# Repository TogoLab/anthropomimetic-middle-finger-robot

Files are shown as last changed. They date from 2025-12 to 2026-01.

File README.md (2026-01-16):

# 人体模倣中指ロボット（Anthropomimetic Middle Finger Robot）

📘 日本語版（このページ）  
🌍 [English](README_EN.md)

---
## 概要

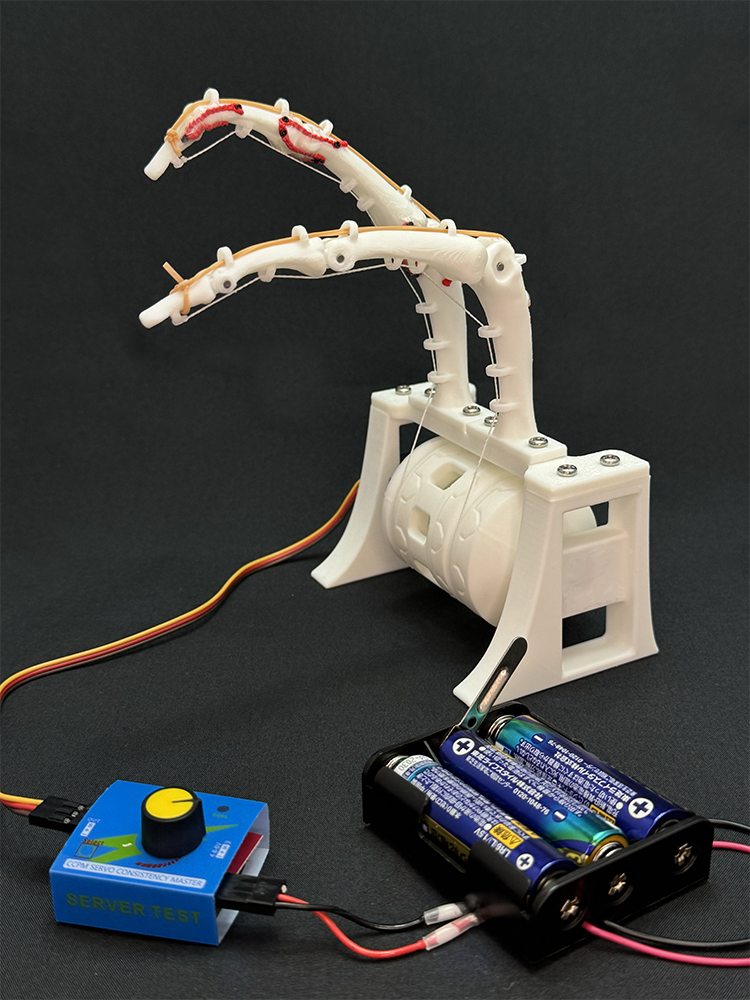
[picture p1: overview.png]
Anthropomimetic Middle Finger Robot


本リポジトリでは、**人体の中指の構造を模倣したロボット指**の  オープンハードウェア設計データを公開しています。

本プロジェクトは、  
- 人体模倣ロボット関節機構と従来ロボット関節機構の比較  
- 人体構造（骨・関節）の理解  
- 教育・体験用途  
を目的として設計されています。

本ロボットは **マイコンやソフトウェアを使用せず**、  
サーボモータ・サーボテスター・電池のみで動作します。  
そのため、ものづくりをしたことがない中学生・高校生でも扱いやすい構成になっています。
「部品を用意するのが大変だ」、「作り方を直接教えてほしい」、「お金がない」という場合には、電気通信大学で開催されている[匠ガールプロジェクトのラボ体験](http://www.ge.uec.ac.jp)や[脳・医工学研究センターのスプリングセミナー](http://blsc.xsrv.jp/)で本ロボットキットの作成体験会を実施していますので、ご参加ください。

東郷研究室では、この人体模倣中指ロボットの作り方を拡張・発展させ、様々な身体部位の人体模倣ロボットの開発に取り組んでいます。本ロボットの作成を面白いと感じたら、是非東郷研究室に参加してください。

---

## 特徴

- 人体（生物）関節を模したモデルと、回転（ロボット）関節モデルの2種類を用意
- ヒトの末節骨〜中手骨までの構造を再現
- 3Dプリント可能なSTLデータと編集可能なCADデータ（STEP）を提供
- 教育用途を想定したシンプルな構成
- ソフトウェア不要（完全ハードウェア）

---

## リポジトリ構成

```
cad/        CADデータ（STEP、F3D）
stl/        3Dプリント用STLデータ
docs/       組み立てマニュアル
licenses/   ライセンス関連ファイル
```

---

## 必要部品（BOM）

必要な部品の一覧は以下を参照してください。

- [部品表（BOM）](./BOM.md)

※ 教育用途を想定しており、同等品・代替品の使用は問題ありません。

---
## 部品の準備

### 樹脂部品の3Dプリント

Bambu Lab A1 miniでの造形を確認しています。
造形パラメータは以下のとおりです。

| フィラメント | Bambu Lab PLA Basic |
| --- | --- |
| 積層ピッチ  | 0.2 mm |
| 充填率 | 15 % |
| インフィル  | グリッド |
| ノズル | 0.4 mm |

### 靭帯の準備

鎖編みを解説する[YouTube動画](https://youtu.be/j-NHvQiJupI?si=Ml5NFn5y3y6gGRWc)などを参考に、PEワイヤを鎖編みします。
[1 mm用のレース針](https://amzn.asia/d/457qnYa)で編んでいます。
端点は結ぶか、ライターで炙って処理します。

---
## 組み立て方法

組み立て手順の詳細は、以下のマニュアルを参照してください。

- 日本語マニュアル：`docs/manual_ja.pdf`

※ 本マニュアルは体験会で配布しているマニュアルを一部改変したものです。本OSH版ではベース（右）の研究室・大学ロゴを削除しています。

---
  
## ライセンス

本リポジトリには、複数のライセンスが適用されています。  
使用する際は、対象ファイルのライセンスを必ず確認してください。

- **骨（人体）モデル**  
  - `/cad/finger_*`,  `/stl/finger_*`  
  - Creative Commons Attribution-ShareAlike 2.1 Japan (CC BY-SA 2.1 JP)  
  - 元データ：[BodyParts3D / ライフサイエンス統合データベースセンター](https://lifesciencedb.jp/bp3d/)

- **土台・プーリー等のオリジナル設計部品**  
  - `/cad/base_*`,  `/stl/base_*`  
  - Creative Commons Attribution 4.0 International (CC BY 4.0)

- **組み立てマニュアル（PDF）**  
  - © Togo Laboratory, All Rights Reserved

詳細は `LICENSE` および `licenses/` フォルダ内のファイルを参照してください。

※ 本リポジトリに含まれる研究室ロゴ・大学ロゴ・名称等は、上記ライセンスの対象外です。これらの使用には、別途許可が必要です。

---

## 注意事項・免責

- 本データは教育・研究用途を目的として提供されています。
- 本ロボットの使用・改造・配布は自己責任で行ってください。
- 可動部による指の挟み込み等に注意してください。
- 本リポジトリの内容を利用したことによるいかなる損害についても、作者は責任を負いません。

---

## 作者・連絡先

東郷 俊太  
電気通信大学大学院情報理工学研究科  
機械知能システム学専攻　准教授  
[ResearchMap](https://researchmap.jp/shuntatogo)
[東郷研究室](http://www.hi.mce.uec.ac.jp/togolab/)
[X](https://twitter.com/togo_lab/)
[Instagram](https://www.instagram.com/togolab_uec/)
[YouTube](https://www.youtube.com/channel/UC10spcvW8-pCTLKy5rrDHyw)

ご質問や不具合報告は GitHub Issues あるいはs.togo[at]uec.ac.jpまで。

東郷研究室では、教育・研究活動へのご支援も歓迎しています。
[電気通信大学基金](https://www.uec.ac.jp/kikin/archives/fund/togolab)

---

## 関連発表

 * 深代 悠太，姜 銀来，横井 浩史，東郷 俊太，“人体模倣母指CM関節の可動域と関節剛性の計測”，第43回日本ロボット学会学術講演会，2D2-01，東京科学大学大岡山キャンパス，2025年9月2–5日．
 * 永嶋 圭佑，姜 銀来，横井 浩史，東郷 俊太，”人体模倣中指ロボットのSim2Realに向けたシミュレーターと実機の開発”，ロボティクス・メカトロニクス講演会2025，2A1-J05，山形ビッグウイング，2025年6月4日–7日．
 * 工藤 陸，姜 銀来，横井 浩史，東郷 俊太，“人体を模倣した流体潤滑を有する指関節構造の粘弾性特性”，第42回日本ロボット学会学術講演会，2J3-06，大阪工業大学梅田キャンパス，2024年9月3–6日．
 * 小畑 承経，姜 銀来，横井 浩史，東郷 俊太，“人体の筋骨格構造を模倣したロボット手指・手首および前腕の開発”，ロボティクス・メカトロニクス講演会2024，2A2-J06，ライトキューブ宇都宮，2024年5月29日–6月1日．
 * 工藤 陸，姜 銀来，横井 浩史，東郷 俊太，“人体を模倣した流体潤滑を有する指関節構造の粘性特性”，ロボティクス・メカトロニクス講演会2024，1A1-D06，ライトキューブ宇都宮，2024年5月29日–6月1日．
 * 小畑 承経，姜 銀来，横井 浩史，東郷 俊太，“人体の筋骨格構造を模倣したロボット手首および前腕の開発” ，第41回日本ロボット学会学術講演会，1B3-02，仙台国際センター，2023年9月11–14日．
 * 工藤 陸，姜 銀来，横井 浩史，東郷 俊太，“人体の関節における液体潤滑を模倣した指関節構造の開発” ，第41回日本ロボット学会学術講演会，1B3-01，仙台国際センター，2023年9月11–14日．

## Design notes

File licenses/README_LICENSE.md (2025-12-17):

# License Guide (日本語)

本リポジトリは、複数のライセンスを組み合わせて構成されています。
使用する際は、対象ファイルに適用されるライセンスを必ず確認してください。

## 骨（人体）モデル
- 対象: cad/finger_* , stl/finger_*
- ライセンス: CC BY-SA 2.1 JP
- 注意:
  - クレジット表示が必要です
  - 改変・再配布時は同一ライセンス（継承）が必要です

## 土台・プーリー等のオリジナル設計部品
- 対象: cad/base_* , stl/base_*
- ライセンス: CC BY 4.0
- 注意:
  - クレジット表示のみ必要
  - 改変・商用利用も可能です

## 組み立てマニュアル
- 対象: docs/*.pdf
- ライセンス: All Rights Reserved
- 注意:
  - 再配布・改変は禁止されています

## ロゴ・名称について
研究室ロゴ、大学ロゴ、名称等は、いずれのライセンスにも含まれません。
使用には別途許可が必要です。

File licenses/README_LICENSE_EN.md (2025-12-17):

# License Guide (English)

This repository is composed of materials distributed under multiple licenses.  
Please make sure to check the license applicable to each file or directory before use.

## Bone (Human Anatomy) Models
- Scope: `cad/finger_*`, `stl/finger_*`
- License: Creative Commons Attribution-ShareAlike 2.1 Japan (CC BY-SA 2.1 JP)
- Notes:
  - Attribution (credit) is required
  - Any modified or redistributed versions must be released under the same license (share-alike)

## Original Design Parts (Base, Pulleys, etc.)
- Scope: `cad/base_*`, `stl/base_*`
- License: Creative Commons Attribution 4.0 International (CC BY 4.0)
- Notes:
  - Attribution is required
  - Modification and commercial use are permitted

## Assembly Manuals
- Scope: `docs/*.pdf`
- License: © Togo Laboratory, All Rights Reserved
- Notes:
  - Redistribution and modification are not permitted

## Logos and Names
Laboratory logos, university logos, names, and trademarks are not covered by any of the above licenses.  
Separate permission is required for their use.

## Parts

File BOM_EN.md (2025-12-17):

# Bill of Materials (BOM)

This document lists the components required to assemble the **Anthropomimetic Middle Finger Robot**.  
The design is intended for educational use, and **equivalent or alternative components may be used without issue**.

The provided links are examples of where components can be obtained and **do not imply endorsement of any specific vendor**.

---

## Required Components

| Manual ID | Component Name | Specification / Notes | Qty | Link |
| --- | --- | --- | --- | --- |
| 1-1 | Battery holder | 3 × AA batteries, with switch | 1 | https://akizukidenshi.com/catalog/g/g112240/ |
| 1-2 | Servo cable | Cut in half before use | 1 | https://amzn.asia/d/8mVq6jo |
| 1-3 | Heat-shrink solder connector | Shrink using heat gun or soldering iron | 2 | https://amzn.asia/d/0xNL0ZV |
| 2 | Controller | Servo tester | 1 | https://amzn.asia/d/4pgGVFi |
| 3 | Servo motor | SG90 | 1 | https://amzn.asia/d/4hQo8Cy |
| 7 | Dry battery | Alkaline AA | 3 | https://amzn.asia/d/7LyDhHT |
| 23,29,32  | Ligament | PE braided wire, size #5 (8 strands), red | 1 | https://amzn.asia/d/2dyn106 |
| 24,30,33  | Joint capsule sheet | Sweat-stain prevention film | 1 | https://amzn.asia/d/8erxhIF |
| 25,35 | Rubber band | Flat length 60 mm | 2 | |
| 26,36 | Muscle wire | PE braided wire, size #5 (8 strands), white | 1 | https://amzn.asia/d/3m2Y8FW |
| 27,37,39  | Tapping screw | M2.5 × 6 mm | 4 | https://amzn.asia/d/fFQeuqP |
| 28,31,34  | Tapping screw | M1 × 3 mm | 24  | https://ja.aliexpress.com/item/1005003207019640.html |
| 43 | Tapping screw | M1 × 3.5 mm | 4 | https://ja.aliexpress.com/item/1005003207019640.html |
| 38 | Shaft | M2 × 10 mm | 3 | https://amzn.asia/d/0ygpu5s |
| 40 | Bolt | M3 × 8 mm | 8 | https://amzn.asia/d/4OWtTQD |
| 41 | Nut | M3 | 8 | https://amzn.asia/d/2O0UdSI |
| 42 | Flanged bushing | 80F-0803 | 1 | https://www.monotaro.com/p/0046/0476/?t.q=80F-0803 |

---

## Tools

*The tools listed below assume a typical hobbyist or educational workshop environment.  
Equivalent tools may be used.*

| Manual ID | Tool Name | Notes | Link |
| --- | --- | --- | --- |
| a | Scissors | Any type | https://www.monotaro.com/p/5375/1733/ |
| b | Mini needle-nose pliers | Optional | https://jp.daisonet.com/products/4549131301625 |
| c | Nippers | Any type | https://ja.aliexpress.com/item/1005006129098627.html |
| d | Precision screwdriver set | Any type | https://jp.daisonet.com/products/4550480360881 |
| e | Darning needle | Optional | https://www.monotaro.com/p/3041/2795 |
| f | Tweezers (curved tip) | Optional | https://jp.daisonet.com/products/4550480538464 |
| g | Diamond file | Any type | https://jp.daisonet.com/products/4979909890288 |
| h | Cloth tape | Any type | https://www.monotaro.com/p/0671/3324/ |
| i | Pincushion | Optional | https://ec.cando-web.co.jp/item/4520297020223/ |
| j | Magnetizer | Optional | https://www.monotaro.com/p/4969/1626 |
| k | Stainless steel tray | Optional | https://jp.daisonet.com/products/4549131589962 |
| l | Magnetic sheet | Optional | https://jp.daisonet.com/products/4550480675473 |
| m | Cutting mat | Optional | https://www.monotaro.com/p/4310/0296 |

---

*This bill of materials is provided for educational and research purposes only.*  
*The authors and affiliated institutions assume no responsibility for any damage or loss resulting from the use of this document.*

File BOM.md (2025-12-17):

# 部品表（BOM）

このドキュメントは、人体模倣中指ロボットを組み立てるために必要な部品一覧です。  
教育用途を想定しており、**同等品・代替品の使用は問題ありません**。
リンク先は入手例として示したものであり、特定の販売元を推奨するものではありません。

---

## 必須部品

| マニュアル部品番号 | 部品名 | 仕様、備考 | 数量  | リンク |
| --- | --- | --- | --- | --- |
| 1-1 | 電池ボックス | 単３電池×3、スイッチ付き | 1 | https://akizukidenshi.com/catalog/g/g112240/ |
| 1-2 | サーボケーブル | 半分に切って使う | 1 | https://amzn.asia/d/8mVq6jo |
| 1-3 | 熱収縮はんだコネクタ | ヒートガンやはんだこてで収縮  | 2 | https://amzn.asia/d/0xNL0ZV |
| 2 | コントローラ | サーボテスター | 1 | https://amzn.asia/d/4pgGVFi |
| 3 | サーボモータ | SG90 | 1 | https://amzn.asia/d/4hQo8Cy |
| 7 | 乾電池 | アルカリ、単３ | 3 | https://amzn.asia/d/7LyDhHT |
| 23、29、32  | 靭帯 | 8本編5号のPEワイヤ（赤色） | 1 | https://amzn.asia/d/2dyn106 |
| 24、30、33  | 関節包シート | 汗ジミ防止フィルム | 1 | https://amzn.asia/d/8erxhIF |
| 25、35 | 輪ゴム | 折径60mm | 2 | |
| 26、36 | 筋ワイヤ | 8本編5号のPEワイヤ（白色） | 1 | https://amzn.asia/d/3m2Y8FW |
| 27、37、39  | タッピングネジ | M2.5 x 6mm | 4 | https://amzn.asia/d/fFQeuqP |
| 28、31、34  | タッピングネジ | M1 x 3 | 24  | https://ja.aliexpress.com/item/1005003207019640.html |
| 43 | タッピングネジ | M1 x 3.5 | 4 | https://ja.aliexpress.com/item/1005003207019640.html |
| 38 | シャフト | M2 x 10mm | 3 | https://amzn.asia/d/0ygpu5s |
| 40 | ボルト | M3 x 8mm | 8 | https://amzn.asia/d/4OWtTQD |
| 41 | ナット | M3 | 8 | https://amzn.asia/d/2O0UdSI |
| 42 | フランジブッシュ | 80F-0803 | 1 | https://www.monotaro.com/p/0046/0476/?t.q=80F-0803 |

---

## 工具

※ 工具は一般的な工作環境を想定した例であり、同等の工具があれば問題ありません。

| マニュアル番号 | 工具名 | 備考 | リンク |
| --- | --- | --- | --- |
| a | はさみ | なんでも良い | https://www.monotaro.com/p/5375/1733/ |
| b | ミニラジオペンチ  | あると便利  | https://jp.daisonet.com/products/4549131301625 |
| c | ニッパー | なんでも良い | https://ja.aliexpress.com/item/1005006129098627.html |
| d | 精密ドライバー | なんでも良い | https://jp.daisonet.com/products/4550480360881 |
| e | とじ針 | あると便利  | https://www.monotaro.com/p/3041/2795 |
| f | ピンセット鷲口 | あると便利  | https://jp.daisonet.com/products/4550480538464 |
| g | ダイヤモンドやすり | なんでも良い | https://jp.daisonet.com/products/4979909890288 |
| h | 布テープ | なんでも良い | https://www.monotaro.com/p/0671/3324/ |
| i | ピンクッション | なくても良い | https://ec.cando-web.co.jp/item/4520297020223/ |
| j | マグネタイザー | なくても良い | https://www.monotaro.com/p/4969/1626 |
| k | ステンレストレー  | なくても良い | https://jp.daisonet.com/products/4549131589962 |
| l | マグネットシート  | なくても良い | https://jp.daisonet.com/products/4550480675473 |
| m | カッターマット | なくても良い | https://www.monotaro.com/p/4310/0296/ |

※ 本部品表は教育・研究用途を目的として公開されています。
※ 本部品表の使用により生じたいかなる損害についても、著者および所属機関は責任を負いません。

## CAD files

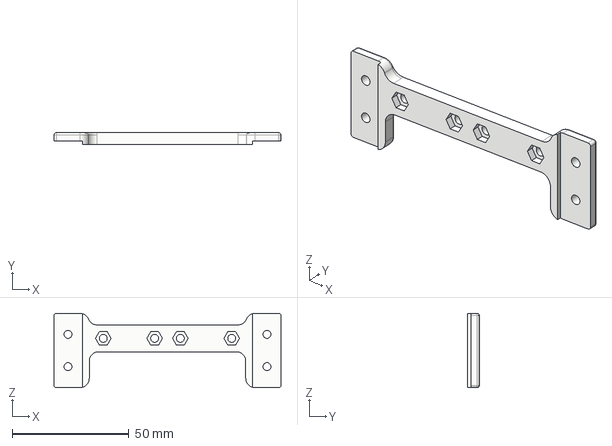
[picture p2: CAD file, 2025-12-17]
cad/base_center_plate_v1.step
97.2 x 5.00 x 31.8 mm

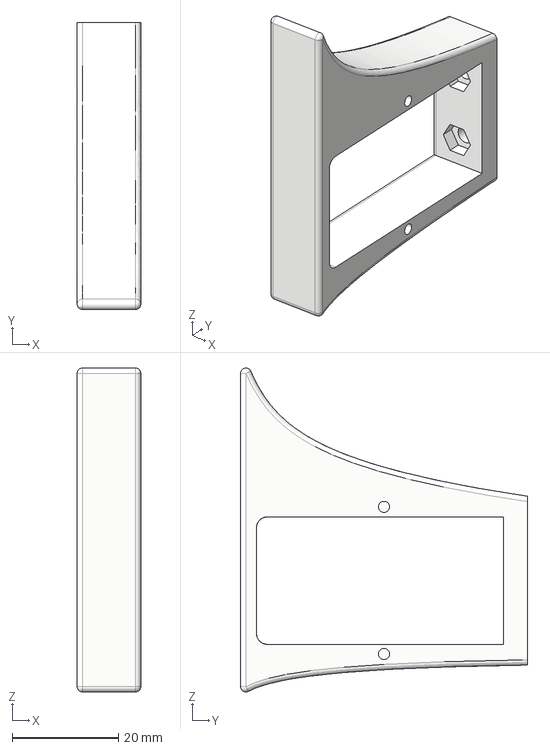
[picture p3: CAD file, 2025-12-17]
cad/base_left_foot_v1.step
12.0 x 54.0 x 61.0 mm

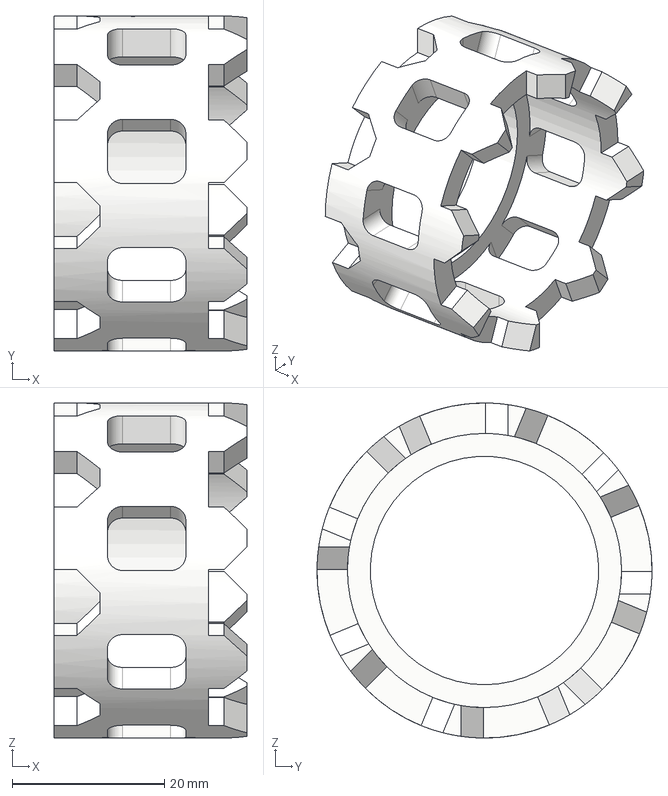
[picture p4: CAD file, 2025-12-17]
cad/base_pulley_2_v1.step
25.3 x 44.0 x 44.0 mm

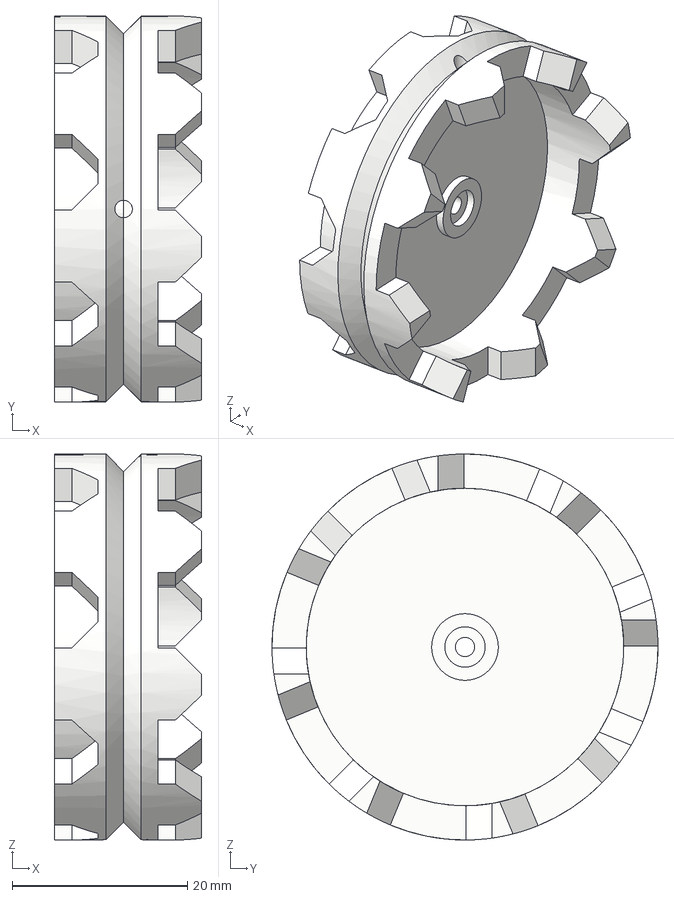
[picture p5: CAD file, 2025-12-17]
cad/base_pulley_3_v1.step
16.8 x 44.0 x 44.0 mm

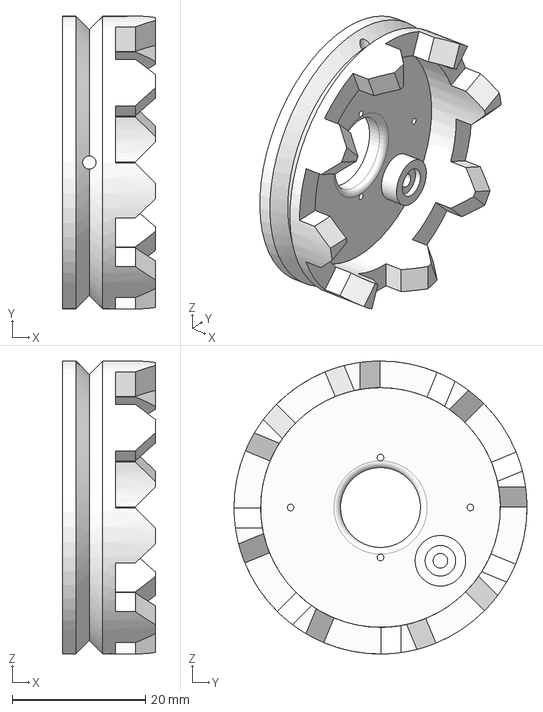
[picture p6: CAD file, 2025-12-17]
cad/base_pulley_1_v1.step
13.9 x 44.0 x 44.0 mm

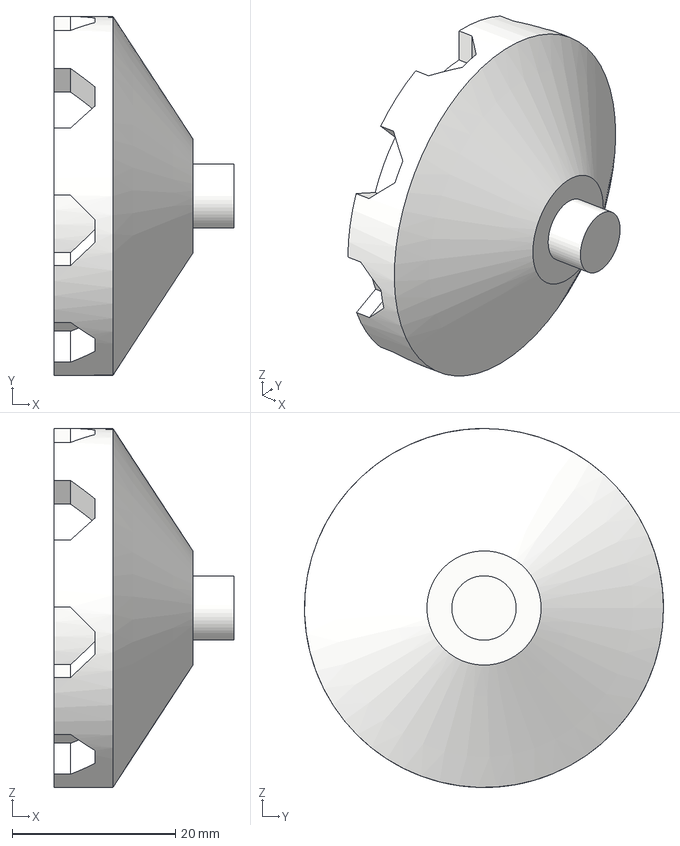
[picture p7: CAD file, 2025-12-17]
cad/base_pulley_4_v1.step
22.0 x 44.0 x 44.0 mm

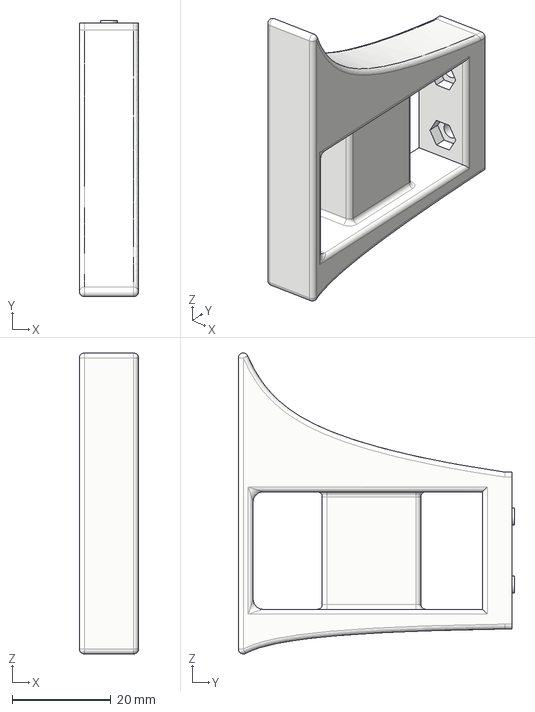
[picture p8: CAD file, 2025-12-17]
cad/base_right_foot_v1.step
12.0 x 56.0 x 61.0 mm

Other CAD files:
cad/base_center_plate_v1.f3d
cad/base_left_foot_v1.f3d
cad/base_pulley_1_v1.f3d
cad/base_pulley_2_v1.f3d
cad/base_pulley_3_v1.f3d
cad/base_pulley_4_v1.f3d
cad/base_right_foot_v1.f3d
cad/finger_human_middle_phalanx_v1.f3d
stl/base_center_plate_v1.stl
stl/base_left_foot_v1.stl
stl/base_pulley_1_v1.stl
stl/base_pulley_2_v1.stl
stl/base_pulley_3_v1.stl
stl/base_pulley_4_v1.stl
stl/base_right_foot_v1.stl
